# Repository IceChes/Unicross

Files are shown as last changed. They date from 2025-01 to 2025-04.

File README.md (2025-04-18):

# Unicross
Unicross is a simple 180mm cross-gantry 3d printer. It was designed to fill a niche - that being cheap cross gantry printers. The BOM cost was about $400 as of 2024, making this printer a good replacement for a Prusa Mini or other similar machine. 

Version 2 is the current usable version. Version 1 is deprecated.



There is no assembly guide, because I made this machine primarily for myself, but there are attached STEP files for the toolhead and main assembly to reference off of. A BOM is completed. I recommend you open the toolhead and assembly STEP files in your favorite CAD software and use the built-in tools to explore the model during assembly.

When I built this machine it cost about $400-450. However, the fluctuating prices of goods during the current trade crisis means I cannot provide an estimate of cost. Proceed with caution.

https://cad.onshape.com/documents/c27a3c37a85bf871058d970a/w/8efdc285a080f347fddd0032/e/d65661c6b902910ffd47d532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

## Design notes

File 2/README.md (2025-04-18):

# Printed Parts Guide

MINIMUM RECOMMENDED SETTINGS:
- Walls: 4
- Top layers: 4
- Bottom layers - 3
- Infill - 20% 3D infill (such as cubic, gyroid, etc)

# Parts
- Bed Knob: use a non-creeping filament at 100% infill. Pause the print to insert a nut. You can check the exact layer in your slicer.
- All Bed Mounting Parts: use a non-creeping filament and at least minimum settings. The BEARING HOLDER and BED MOUNT are both intended to be printed laying down on their sides.
- BLTouch Mount: use a non-creeping filament resistant to at least 60C and 100% infill.
- Bracket Plate: Use a non-creeping filament and at least minimum settings.
- Corner Bracket: Use a non-creeping filament and at least minimum settings.
- Foot: Use a non-creeping filament and at least minimum settings. You may wish to add bottom layers for extra ruggedness.
- LCD Mount: Use any filament at any sufficiently strong settings.
- Limiters: Use a non-creeping filament and at least minimal settings.
- Long and Short Mounts: Use a non-creeping filament resistant to at least 60C, 6 walls, 6 top layers, and 3 bottom layers with 40% 3D infill.
- Paneling Parts: Use any filament and sufficiently strong settings.
- Rod Block: Use any non-creeping filament with 6 walls, 6 top layers, 6 bottom layers, and 60% 3D infill.
- Tensioner: Use any non-creeping filament and 100% infill. Ensure very good layer adhesion.
- Toolhead Cable Clamp: Use any filament with at least minimal settings.
- Toolhead Hotend Clamp: Use any filament resistant to at least 60C and minimal settings.
- Toolhead: Use any filament resistant to at least 60C, 6 walls, 6 top layers, 6 bottom layers, and 40% 3D infill.
- Z Arm: Use any non-creeping filament with at least minimal settings.
- Z Motor Mount: Use any non-creeping filament resistant to at least 60C and minimal settings.

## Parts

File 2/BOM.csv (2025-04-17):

Part | Quant. | Link
2020 extrusion 350mm | 8 | https://www.aliexpress.us/item/3256805051854714.html
KP3S bed | 1 | N/A (I genuinely do not know where to buy these since Kingroon discontinued the KP3s)
4240 motor | 5 | https://www.amazon.com/STEPPERONLINE-Stepper-63-74oz-Connector-Extruder/dp/B07LCHHQ97
LM8UU bearing | 8 | https://www.aliexpress.us/item/2251832657203612.html
LM8LUU bearing | 2 | https://www.aliexpress.us/item/2255800936019514.html
250x8mm linear rod | 4 | https://www.aliexpress.us/item/3256801194605508.html
300x8mm linear rod | 6 | https://www.aliexpress.us/item/3256801194605508.html
T8 nut | 2 | N/A (included with leadscrew)
T8 leadscrew 250mm | 2 | https://www.aliexpress.us/item/2255801146318191.html
GT2 belt | ~5M | https://www.aliexpress.us/item/3256806120793282.html
750mm GT2 belt | 1 | https://www.aliexpress.us/item/3256804262911780.html
20T 5mm bore GT2 pulley | 5 | https://www.aliexpress.us/item/2251832808788159.html
20T 5mm bore GT2 idler | 6 | https://www.aliexpress.us/item/2251832539995194.html
180mm PEI sheet | 1 | https://www.aliexpress.us/item/3256805641662701.html
30T 8mm bore GT2 pulley | 2 | https://www.aliexpress.us/item/3256805593092055.html
608 bearing | 2 | https://www.aliexpress.us/item/3256801626904419.html
Electronic component | Quant. | Link
BigTreeTech SKR E3 Mini 3.0 | 1 | https://www.aliexpress.us/item/3256805861115217.html
Meanwell LRS-350-24 | 1 | https://www.aliexpress.us/item/3256806958274247.html
Raspberry Pi <2-5> | 1 | N/A (please check for availability in various places)
IEC fused power socket | 1 | https://www.aliexpress.us/item/2251832643407093.html
16awg stranded wire | N/A | N/A (everyone has their favorite brand or own supply)
22awg stranded wire | N/A | N/A (everyone has their favorite brand or own supply)
Buck converter | 1 | https://www.aliexpress.us/item/3256804718557368.html
Fan MOSFET [optional] | 1 | https://www.aliexpress.us/item/3256805264005227.html
Parallel board | 2 | https://www.aliexpress.us/item/3256803393452783.html
Stepper cable | 5 | https://www.aliexpress.us/item/3256804466627797.html
Toolhead component | Quant. | Link
Dragon hotend | 1 | https://www.aliexpress.us/item/3256804340965950.html
Sherpa mini extruder | 1 | https://www.aliexpress.us/item/3256802301412640.html
4010 blower fan | 2 | https://www.aliexpress.us/item/2251832612319325.html
Cartridge thermistor | 1 | https://www.aliexpress.us/item/3256805987471638.html
24V heater cartridge | 1 | https://www.aliexpress.us/item/2251832630477143.html
4010 axial fan | 1 | https://www.aliexpress.us/item/3256804770149410.html
BLTouch (or substitute) | 1 | https://www.aliexpress.us/item/2251832763135773.html
Hardware piece
M5x10 bolt | 2 packs | https://www.aliexpress.us/item/2251832708216186.html
M5 nut | 1 pack | https://www.aliexpress.us/item/3256803624749385.html
M5 T-nut | 3 packs | https://www.aliexpress.us/item/3256801437020797.html
M3 screw set | 1 | https://www.aliexpress.us/item/3256806736020361.html

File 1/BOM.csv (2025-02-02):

Part | Quant. | Unit. | Ext. | Link
2020 extrusion 350mm | 8 | $13.45/4 | 26.9 | https://www.aliexpress.us/item/3256805051854714.html
KP3S bed | 1 | $22.99/1 | 22.99 | https://www.aliexpress.us/item/2255800343160168.html
4240 motor | 5 | $48/5 | 48 | https://www.amazon.com/STEPPERONLINE-Stepper-63-74oz-Connector-Extruder/dp/B07LCHHQ97
LM8UU bearing | 8 | $6.70/4 | 13.4 | https://www.aliexpress.us/item/2251832657203612.html
LM8LUU bearing | 2 | $7.16/2 | 7.16 | https://www.aliexpress.us/item/2255800936019514.html
250x8mm linear rod | 4 | $3.36/1 | 13.44 | https://www.aliexpress.us/item/3256801194605508.html
300x8mm linear rod | 6 | $4.04/1 | 24.24 | https://www.aliexpress.us/item/3256801194605508.html
T8 nut | 2 |  |  | N/A (included with leadscrew)
T8 leadscrew 250mm | 2 | $3.69/1 | 7.38 | https://www.aliexpress.us/item/2255801146318191.html
GT2 belt | ~5M | $11.99/5M | 11.99 | https://www.aliexpress.us/item/3256806120793282.html
730mm GT2 belt | 1 | $1.42 | 1.42 | https://www.aliexpress.us/item/3256804262911780.html
20T 5mm bore GT2 pulley | 5 | $6.79/5 | 6.79 | https://www.aliexpress.us/item/2251832808788159.html
20T 5mm bore GT2 idler | 6 | $15.29/10 | 15.29 | https://www.aliexpress.us/item/2251832539995194.html
180mm PEI sheet [optional, bed comes with a sheet] | 1 | $15.36/1 | 15.36 | https://www.aliexpress.us/item/3256805641662701.html
30T 8mm bore GT2 pulley | 2 | $2/1 | 4 | https://www.aliexpress.us/item/3256805593092055.html
608 bearing | 2 | $2.66/10 | 2.66 | https://www.aliexpress.us/item/3256801626904419.html
Electronic component | Quant. | Unit. | Ext. | Link
BigTreeTech SKR E3 Mini 3.0 | 1 | $29.40//1 | 29.4 | https://www.aliexpress.us/item/3256805861115217.html
Meanwell LRS-350-24 | 1 | $37.58/1 | 37.58 | https://www.aliexpress.us/item/3256806958274247.html
Raspberry Pi <2-5> | 1 | $35/1 | 35 | N/A (please check for availability in various places)
IEC fused power socket | 1 | $1.39/1 | 1.39 | https://www.aliexpress.us/item/2251832643407093.html
16awg stranded wire | N/A |  |  | N/A (everyone has their favorite brand or own supply)
22awg stranded wire | N/A |  |  | N/A (everyone has their favorite brand or own supply)
Buck converter | 1 | $1.25/1 | 1.25 | https://www.aliexpress.us/item/3256804718557368.html
Fan MOSFET [optional] | 1 | $1.12/1 | 1.12 | https://www.aliexpress.us/item/3256805264005227.html
Parallel board | 2 | $3.3/4 | 3.3 | https://www.aliexpress.us/item/3256803393452783.html
Stepper cable | 5 | $1.60/4 | 5.2 | https://www.aliexpress.us/item/3256804466627797.html
Toolhead component | Quant. | Unit. | Ext. | Link
Dragon hotend | 1 | $17.34/1 | 17.34 | https://www.aliexpress.us/item/3256804340965950.html
Sherpa mini extruder | 1 | $33.73/1 | 33.73 | https://www.aliexpress.us/item/3256802301412640.html
4010 blower fan | 2 | $13.09/2 | 13.09 | https://www.aliexpress.us/item/2251832612319325.html
Cartridge thermistor | 1 | $1.76/2 | 1.76 | https://www.aliexpress.us/item/3256805987471638.html
24V heater cartridge | 1 | $3.07/1 | 3.07 | https://www.aliexpress.us/item/2251832630477143.html
4010 axial fan | 1 | $4.17/1 | 4.17 | https://www.aliexpress.us/item/3256804770149410.html
BLTouch (or substitute) | 1 | $10.94/1 | 10.94 | https://www.aliexpress.us/item/2251832763135773.html
Hardware piece
M5x10 bolt | 2 packs | $4.62/pck | 9.24 | https://www.aliexpress.us/item/2251832708216186.html
M5 nut | 1 pack | $3.69/pck | 3.69 | https://www.aliexpress.us/item/3256803624749385.html
M5 T-nut | 3 packs | $1.42/pck | 4.26 | https://www.aliexpress.us/item/3256801437020797.html
M3 screw set | 1 | $5/1 | 5 | https://www.aliexpress.us/item/3256806736020361.html
 |  |  | 419.87

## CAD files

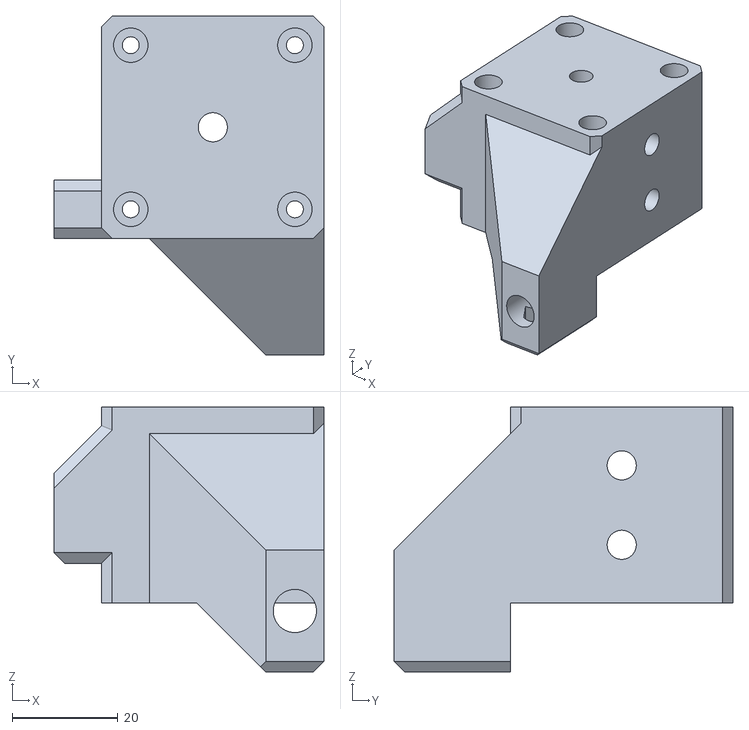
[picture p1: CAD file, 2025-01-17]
1/Files/STL/Motor Mount - Short Mount.stl
51.0 x 64.0 x 50.0

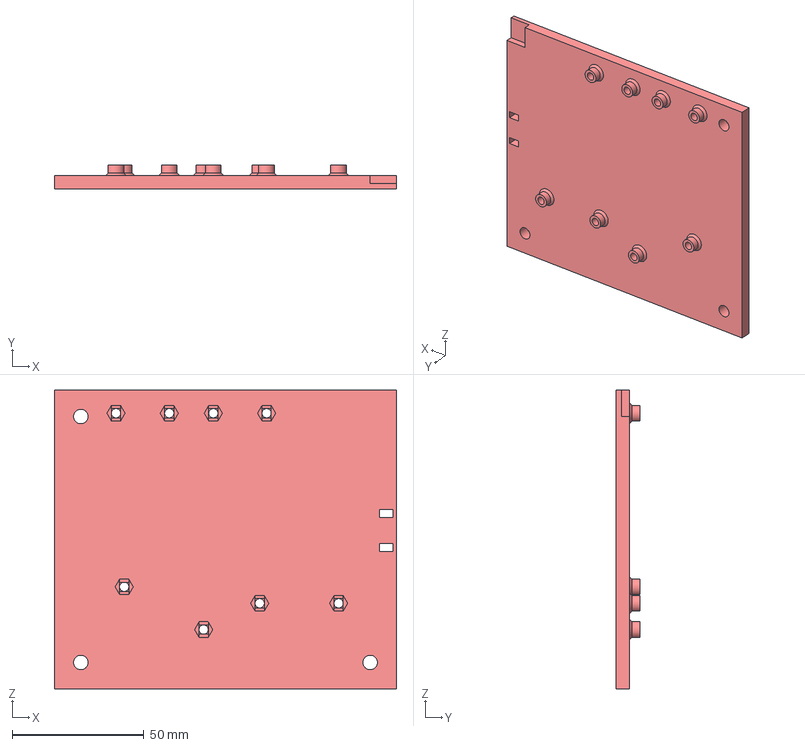
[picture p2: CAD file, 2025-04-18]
2/Files/Paneling - Bottom Right.step
130.0 x 9.00 x 113.5 mm

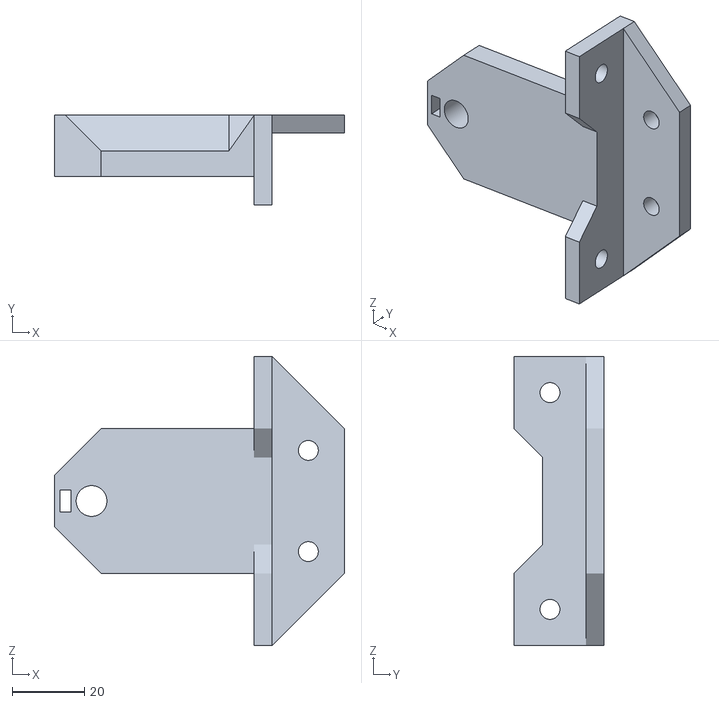
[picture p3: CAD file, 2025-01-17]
1/Files/STL/Z Rod Arm.stl
80.2 x 25.0 x 80.0

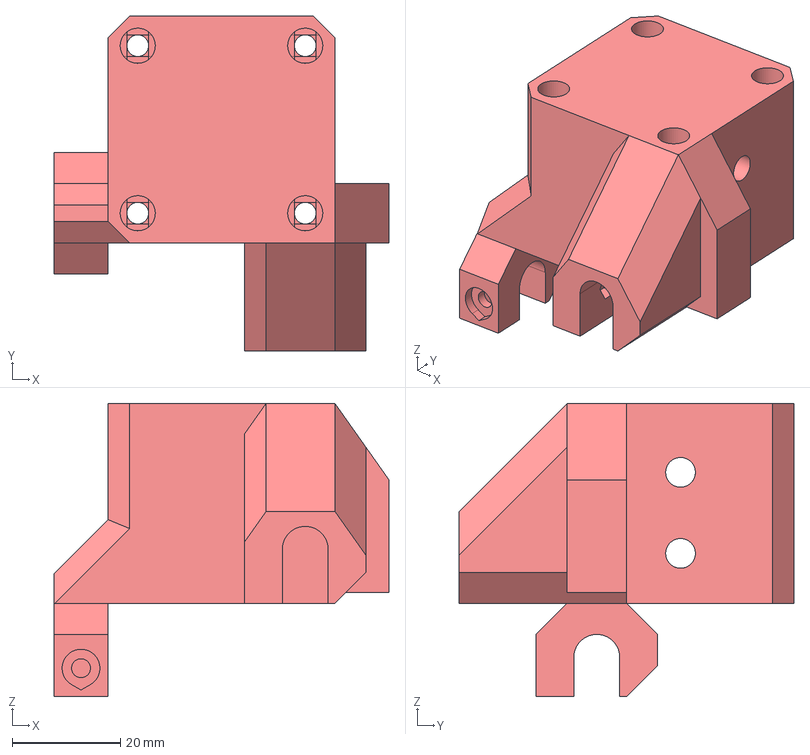
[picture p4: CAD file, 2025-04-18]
2/Files/Short Mount.step
62.0 x 62.0 x 54.2 mm

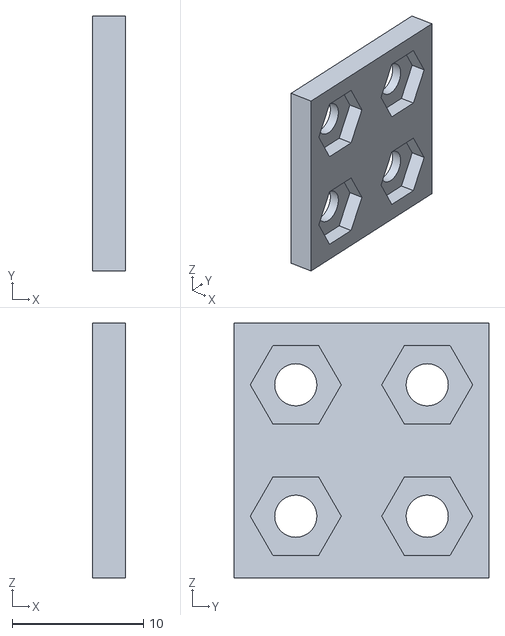
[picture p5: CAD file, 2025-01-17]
1/Files/STL/Panelling - Connector.stl
2.50 x 19.4 x 19.4

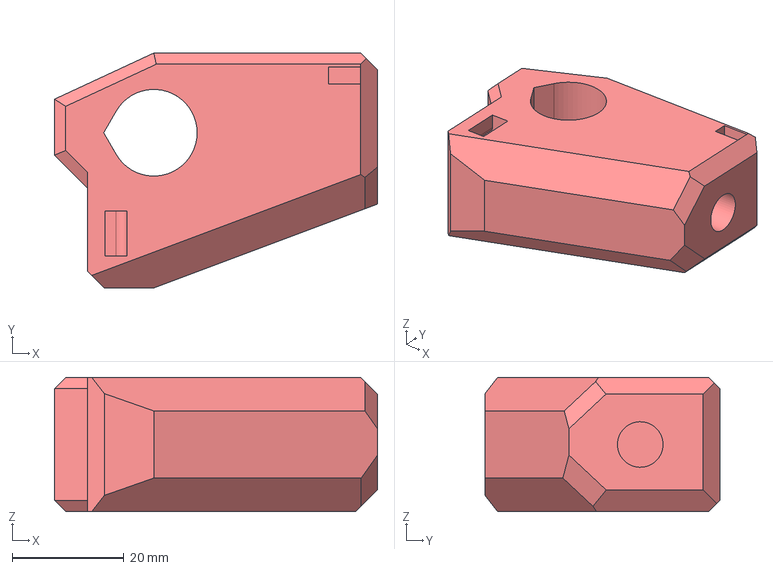
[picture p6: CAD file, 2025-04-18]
2/Files/Rod Block.step
57.8 x 42.0 x 24.0 mm

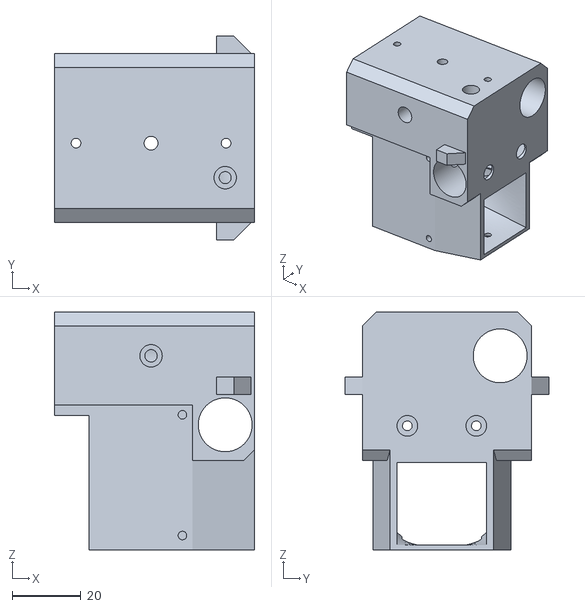
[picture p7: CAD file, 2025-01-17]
1/Files/STL/Toolhead.stl
58.0 x 59.0 x 69.0

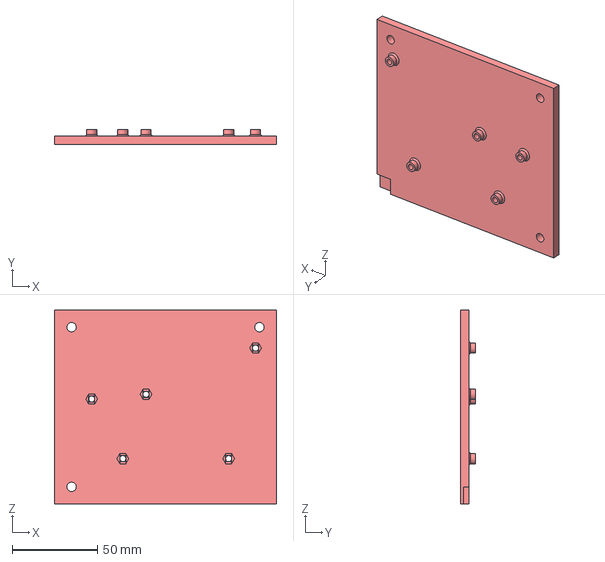
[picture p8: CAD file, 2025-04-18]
2/Files/Paneling - Top Right.step
130.0 x 9.00 x 113.5 mm

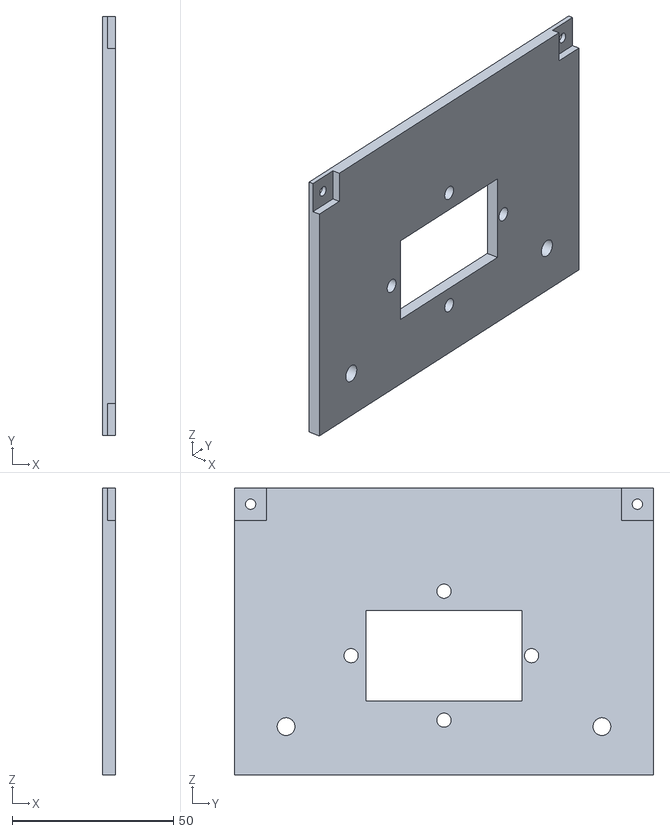
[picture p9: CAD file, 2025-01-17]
1/Files/STL/Panelling - Bottom Mid.stl
4.00 x 130.0 x 89.0

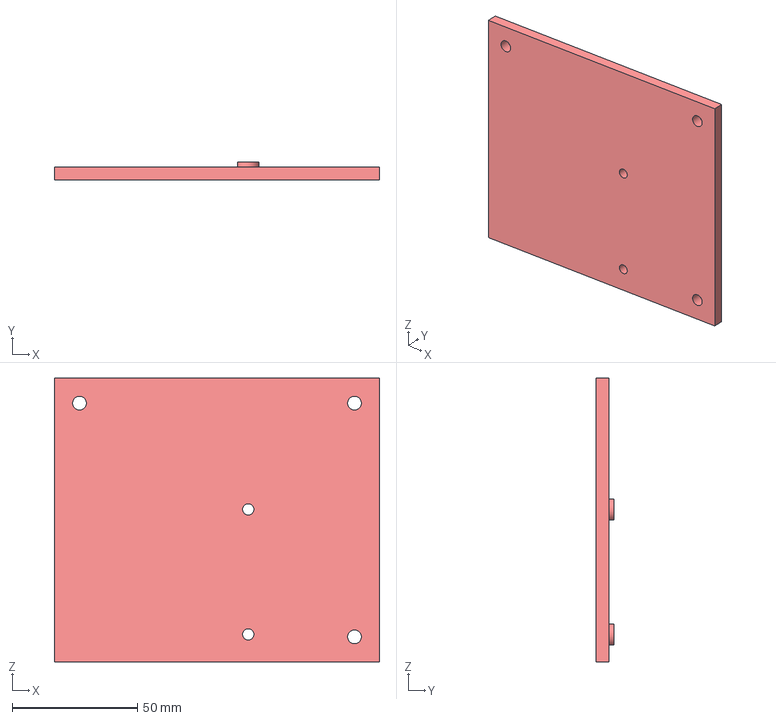
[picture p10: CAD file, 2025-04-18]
2/Files/Paneling - Top Left.step
130.0 x 7.00 x 113.5 mm

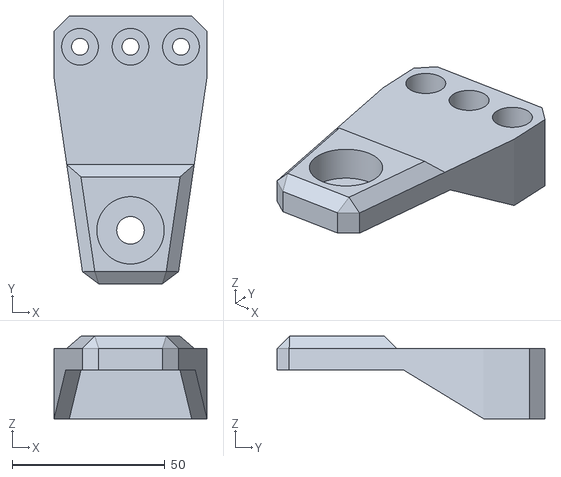
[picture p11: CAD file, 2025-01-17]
1/Files/STL/Z Axis - Bearing Block.stl
50.0 x 87.5 x 27.0

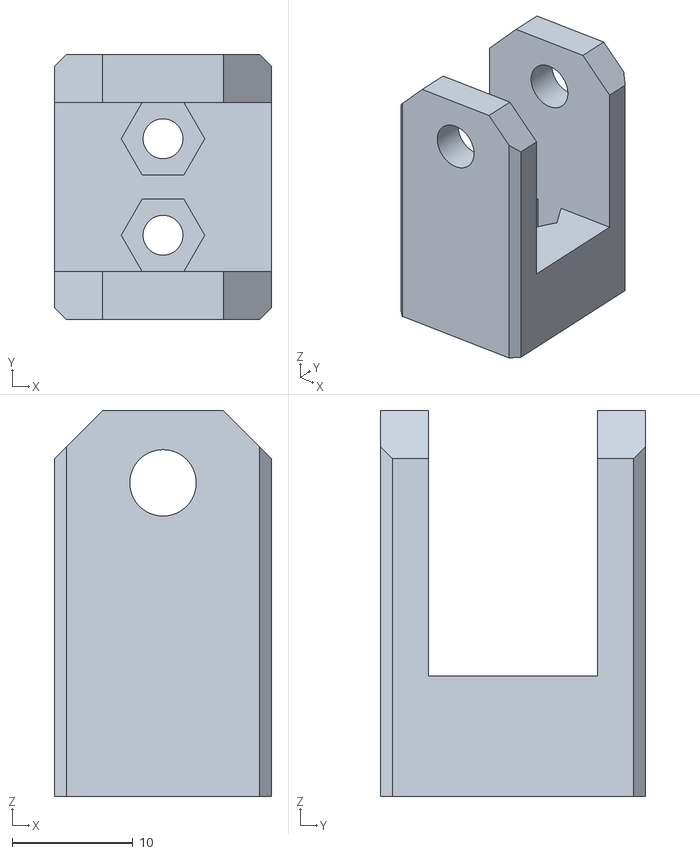
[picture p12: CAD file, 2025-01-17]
1/Files/STL/XY Tensioner.stl
18.0 x 22.0 x 32.0

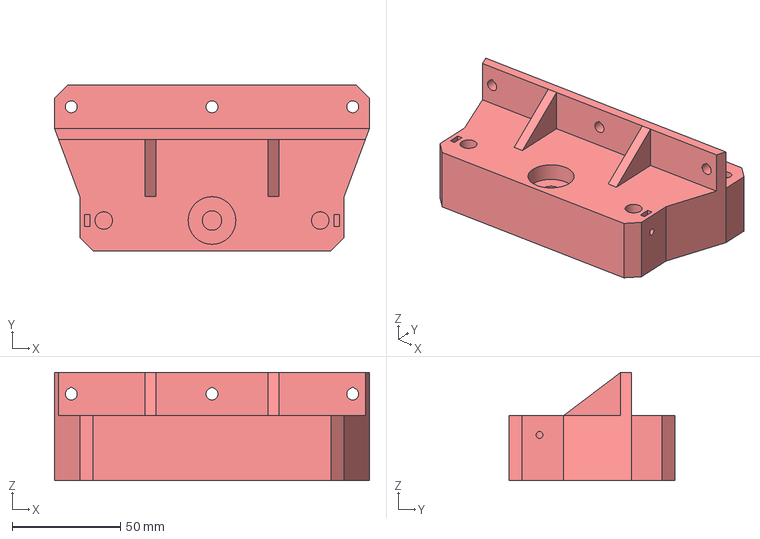
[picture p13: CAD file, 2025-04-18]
2/Files/Bed Mounting - Base Block.step
145.5 x 76.5 x 50.0 mm

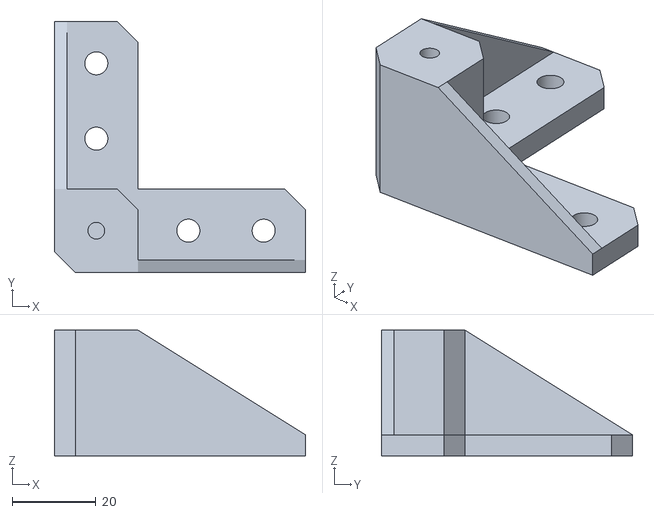
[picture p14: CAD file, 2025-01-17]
1/Files/STL/Foot.stl
60.0 x 60.0 x 30.0

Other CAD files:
2/Files/Paneling - Top Mid.step
2/Files/Paneling - Bottom Left.step
1/Files/STL/BLTouch Mount.stl
2/Files/Paneling - Bottom Mid.step
1/Files/STL/4010 Blower - Duct - Left.stl
1/Files/STL/4010 Blower - Duct - Right.stl
1/Files/STL/Corner Bracket.stl
1/Files/STL/LM8UU - Rod Block.stl
1/Files/STL/Motor Mount - Long Mount.stl
1/Files/STL/Panelling - Bottom Left.stl
1/Files/STL/Panelling - Bottom Right.stl
1/Files/STL/Panelling - Panel Bracket.stl
1/Files/STL/Panelling - Top Left.stl
1/Files/STL/Panelling - Top Mid.stl
1/Files/STL/Panelling - Top Right.stl
1/Files/STL/Toolhead Hotend Clamp.stl
1/Files/STL/Z Axis - Bed Bracket.stl
1/Files/STL/Z Axis - Z Base Block.stl
1/Files/STL/Z Motor Mount.stl
2/Files/BLTouch Mount.step
2/Files/Bed Knob.step
2/Files/Bed Mounting - Bearing Holder.step
2/Files/Bed Mounting - Bed Mount.step
2/Files/Bracket Plate.step
2/Files/Corner Bracket.step
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

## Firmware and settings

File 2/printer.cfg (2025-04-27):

[include macros.cfg]
[include mainsail.cfg]
[virtual_sdcard]
path: /home/pi/printer_data/gcodes
on_error_gcode: CANCEL_PRINT

[stepper_x]
step_pin: PB13
dir_pin: !PB12
enable_pin: !PB14
microsteps: 16
rotation_distance: 40
position_endstop: -6
position_max: 185
position_min: -6
homing_speed: 20
endstop_pin: tmc2209_stepper_x:virtual_endstop
homing_retract_dist: 0

[tmc2209 stepper_x]
uart_pin: PC11
tx_pin: PC10
uart_address: 0
run_current: 1
interpolate: False
stealthchop_threshold: 999999
diag_pin: ^PC0
driver_SGTHRS: 26

[stepper_y]
step_pin: PB10
dir_pin: PB2
enable_pin: !PB11
microsteps: 16
rotation_distance: 40
position_endstop: -3
position_max: 185
position_min: -3
homing_speed: 20
endstop_pin: tmc2209_stepper_y:virtual_endstop
homing_retract_dist: 0

[tmc2209 stepper_y]
uart_pin: PC11
tx_pin: PC10
uart_address: 2
run_current: 1
interpolate: False
stealthchop_threshold: 999999
diag_pin: ^PC1
driver_SGTHRS: 26

[stepper_z]
step_pin: PB0
dir_pin: !PC5
enable_pin: !PB1
microsteps: 16
rotation_distance: 8
endstop_pin: probe:z_virtual_endstop
#position_endstop: 0.0
position_max: 250
position_min: -10
homing_speed: 10
gear_ratio: 3:2

[tmc2209 stepper_z]
uart_pin: PC11
tx_pin: PC10
uart_address: 1
run_current: 1
interpolate: True
stealthchop_threshold: 0

[extruder]
step_pin: PB3
dir_pin: !PB4
enable_pin: !PD1
microsteps: 8
rotation_distance: 22.68776
gear_ratio: 50:8
nozzle_diameter: 0.4
filament_diameter: 1.75
heater_pin: PC8
sensor_type: ATC Semitec 104GT-2
sensor_pin: PA0
#control: pid
#pid_Kp: 21.527
#pid_Ki: 1.063
#pid_Kd: 108.982
min_temp: 0
max_temp: 300
max_extrude_only_distance: 1000
pressure_advance: 0.0925

[tmc2209 extruder]
uart_pin: PC11
tx_pin: PC10
uart_address: 3
run_current: 0.7
stealthchop_threshold: 999999

[heater_bed]
heater_pin: PC9
sensor_type: ATC Semitec 104GT-2
sensor_pin: PC4
#control: pid
#pid_Kp: 54.027
#pid_Ki: 0.770
#pid_Kd: 948.182
min_temp: 0
max_temp: 130

[heater_fan nozzle_cooling_fan]
pin: PC6

[fan]
pin: PC7

[mcu]
serial: /dev/serial/by-id/usb-Klipper_stm32g0b1xx_4100290008504B5735313920-if00

[printer]
kinematics: cartesian
max_velocity: 250
max_accel: 1000
max_z_velocity: 15
max_z_accel: 100
square_corner_velocity: 30


[bltouch]
sensor_pin: ^PC14
control_pin: PA1
stow_on_each_sample: False
probe_with_touch_mode: True
pin_up_reports_not_triggered: True
pin_up_touch_mode_reports_triggered: True

x_offset: 0
y_offset: 37.5
#z_offset: 0

[verify_heater extruder]
max_error: 300
check_gain_time: 90
hysteresis: 8
heating_gain: 2

[bed_mesh]
speed: 300
horizontal_move_z: 8
mesh_min: 40, 40
mesh_max: 140, 140
probe_count: 5, 5
mesh_pps: 3, 3
algorithm: bicubic
fade_start: 1
fade_end: 10
fade_target: 0

[homing_override]
gcode:

    FORCE_MOVE STEPPER=stepper_z DISTANCE=3 VELOCITY=10 
    
    SET_TMC_CURRENT STEPPER=stepper_x CURRENT=1.000
    SET_TMC_CURRENT STEPPER=stepper_y CURRENT=1.000

    G28 Y
    G1 Y10
    G28 X 
    G1 X10
    G1 X90 Y52.5 ; Change the X and Y coordinates to the center of your print bed
    G28 Z
    
    SET_TMC_CURRENT STEPPER=stepper_x CURRENT=1.400
    SET_TMC_CURRENT STEPPER=stepper_y CURRENT=1.400 


[display]
lcd_type: st7920
cs_pin: EXP1_7
sclk_pin: EXP1_6
sid_pin: EXP1_8
encoder_pins: ^EXP1_5, ^EXP1_3
click_pin: ^!EXP1_2

[board_pins]
aliases:

    EXP1_1=PB5,  EXP1_3=PA9,   EXP1_5=PA10, EXP1_7=PB8, EXP1_9=<GND>,
    EXP1_2=PA15, EXP1_4=<RST>, EXP1_6=PB9,  EXP1_8=PD6, EXP1_10=<5V>

[force_move]
enable_force_move = true

[idle_timeout]
gcode:
  m84
timeout: 64800

[exclude_object]

[respond]
default_type: echo
default_prefix: echo:

[save_variables]
filename: ~/printer_data/config/variables.cfg

[pause_resume]
recover_velocity: 300

#*# <---------------------- SAVE_CONFIG ---------------------->
#*# DO NOT EDIT THIS BLOCK OR BELOW. The contents are auto-generated.
#*#
#*# [extruder]
#*# control = pid
#*# pid_kp = 18.981
#*# pid_ki = 1.291
#*# pid_kd = 69.754
#*#
#*# [bltouch]
#*# z_offset = 2.400
#*#
#*# [bed_mesh default]
#*# version = 1
#*# points =
#*# 	0.068333, 0.079167, 0.077500, 0.088333, 0.095833
#*# 	0.052500, 0.035833, 0.056667, 0.050833, 0.041667
#*# 	0.002500, -0.014167, -0.008333, -0.012500, -0.005833
#*# 	-0.064167, -0.057500, -0.074167, -0.080000, -0.076667
#*# 	-0.139167, -0.151667, -0.170833, -0.149167, -0.138333
#*# x_count = 5
#*# y_count = 5
#*# mesh_x_pps = 3
#*# mesh_y_pps = 3
#*# algo = bicubic
#*# tension = 0.2
#*# min_x = 40.0
#*# max_x = 140.0
#*# min_y = 40.0
#*# max_y = 140.0
#*#
#*# [heater_bed]
#*# control = pid
#*# pid_kp = 66.213
#*# pid_ki = 1.752
#*# pid_kd = 625.717

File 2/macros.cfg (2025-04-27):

[gcode_macro SMART_HOME]
gcode:
    {% if printer.toolhead.homed_axes != "xyz" %}
        G28
    {% endif %}

[gcode_macro PARK]
description: Park the toolhead at the origin
gcode:
  G90
  G0 X60 Y180 F3000

[gcode_macro CHANGE_FILAMENT_BEGIN]
description: Begin the change filament wizard
gcode:

  {% set svv = printer.save_variables.variables %}
  {% set unload_temp = svv.loaded_filament_temp|default(240)|int %}

  M104 S{unload_temp}
    
  SMART_HOME
    
  PARK

  RESPOND TYPE=echo MSG="Waiting for heat to unload filament."
  
  M109 S{unload_temp}
  M83
  G92 E0
    
  RESPOND TYPE=command MSG="action:prompt_begin Retract filament"
  RESPOND TYPE=command MSG="action:prompt_text Full retract removes filament from the hotend. Small retract removes a bit more if the full retract wasn't enough."
    
  RESPOND TYPE=command MSG="action:prompt_button_group_start"
  RESPOND TYPE=command MSG="action:prompt_button full retract|G0 E-120 F1000|primary"
  RESPOND TYPE=command MSG="action:prompt_button small retract|G0 E-5 F1000|primary"
  RESPOND TYPE=command MSG="action:prompt_button_group_end"
    
  RESPOND TYPE=command MSG="action:prompt_footer_button NEXT|CHANGE_FILAMENT_SELECT|primary"
    
  RESPOND TYPE=command MSG="action:prompt_show"

[gcode_macro CHANGE_FILAMENT_SELECT]
description: Begin the filament select wizard
gcode:
  
  RESPOND TYPE=command MSG=action:prompt_end
  
  RESPOND TYPE=command MSG="action:prompt_begin Select filament"
  RESPOND TYPE=command MSG="action:prompt_text Choose which filament is being loaded. The OTHER option will use 240C as the load/unload temperature."
    
  RESPOND TYPE=command MSG="action:prompt_button_group_start"
  RESPOND TYPE=command MSG="action:prompt_button PLA|SAVE_VARIABLE VARIABLE=loaded_filament_temp VALUE={210}|primary"
  RESPOND TYPE=command MSG="action:prompt_button PETG|SAVE_VARIABLE VARIABLE=loaded_filament_temp VALUE={240}|primary"
  RESPOND TYPE=command MSG="action:prompt_button ABS/ASA|SAVE_VARIABLE VARIABLE=loaded_filament_temp VALUE={250}|primary"
  RESPOND TYPE=command MSG="action:prompt_button_group_end"
  RESPOND TYPE=command MSG="action:prompt_button_group_start"
  RESPOND TYPE=command MSG="action:prompt_button Nylon|SAVE_VARIABLE VARIABLE=loaded_filament_temp VALUE={270}|primary"
  RESPOND TYPE=command MSG="action:prompt_button TPU|SAVE_VARIABLE VARIABLE=loaded_filament_temp VALUE={200}|primary"
  RESPOND TYPE=command MSG="action:prompt_button Other|SAVE_VARIABLE VARIABLE=loaded_filament_temp VALUE={240}|primary"
  RESPOND TYPE=command MSG="action:prompt_button_group_end"
    
  RESPOND TYPE=command MSG="action:prompt_footer_button NEXT|CHANGE_FILAMENT_LOAD|primary"

  RESPOND TYPE=command MSG="action:prompt_show"


[gcode_macro CHANGE_FILAMENT_LOAD]
description: Begin the load filament wizard
gcode:
  
  {% set svv = printer.save_variables.variables %}
  {% set load_temp = svv.loaded_filament_temp|default(240)|int %}

  M104 S{load_temp}

  SMART_HOME
    
  PARK
  
  RESPOND TYPE=command MSG=action:prompt_end
  RESPOND TYPE=echo MSG="Waiting for heat to load filament."

    
  M109 S{load_temp}

  M83
  
  RESPOND TYPE=command MSG="action:prompt_begin Load filament"
  RESPOND TYPE=command MSG="action:prompt_text Push filament up to the extruder gears, then press LOAD. Use PURGE as needed until color is correct."
    
  RESPOND TYPE=command MSG="action:prompt_button_group_start"
  RESPOND TYPE=command MSG="action:prompt_button LOAD|G0 E120 F1000|primary"
  RESPOND TYPE=command MSG="action:prompt_button PURGE|G0 E20 F250|primary"
  RESPOND TYPE=command MSG="action:prompt_button_group_end"
    
  RESPOND TYPE=command MSG="action:prompt_footer_button COOL NOZZLE|M104 S0|primary"

  RESPOND TYPE=command MSG="action:prompt_show"
  
[gcode_macro WLED_ON]
description: Turn WLED strip on using optional preset
gcode:
  {% set strip = params.STRIP|default("chamber")|string %}
  {% set preset = params.PRESET|default(4)|int %}

  {action_call_remote_method("set_wled_state",
                             strip=strip,
                             state=True,
                             preset=preset)}

[gcode_macro WLED_WARM_LIGHT]
description: Switch to the "warm lights" WLED preset
gcode:
  WLED_ON STRIP=chamber PRESET=3

[gcode_macro WLED_COOL_LIGHT]
description: Switch to the "cool lights" WLED preset
gcode:
  WLED_ON STRIP=chamber PRESET=2
                             
[gcode_macro WLED_OFF]
description: Set WLED strip to 0 brightness
gcode:
  WLED_ON STRIP=chamber PRESET=4

[gcode_macro CHANGE_NOZZLE]
description: Initiate a nozzle change
gcode: 

  {% set svv = printer.save_variables.variables %}
  {% set load_temp = svv.nozzle_size|default(0.4)|int %}

  {% set svv = printer.save_variables.variables %}
  {% set unload_temp = svv.loaded_filament_temp|default(240)|int %}
  
  SMART_HOME
  PARK
  G0 Z80 F3000

  RESPOND TYPE=echo MSG="Waiting for heat to unload filament."

  M104 S{unload_temp}
  M109 S{unload_temp}
  
  M83
  G92 E0
  G0 E-10 F1000
  M109 S280

  RESPOND TYPE=command MSG="action:prompt_begin Select nozzle size"
  RESPOND TYPE=command MSG="action:prompt_text Choose a nozzle diameter"
    
  RESPOND TYPE=command MSG="action:prompt_button_group_start"
  RESPOND TYPE=command MSG="action:prompt_button 0.2|SAVE_VARIABLE VARIABLE=nozzle_size VALUE={0.2}|primary"
  RESPOND TYPE=command MSG="action:prompt_button 0.25|SAVE_VARIABLE VARIABLE=nozzle_size VALUE={0.25}|primary"
  RESPOND TYPE=command MSG="action:prompt_button 0.4|SAVE_VARIABLE VARIABLE=nozzle_size VALUE={0.4}|primary"
  RESPOND TYPE=command MSG="action:prompt_button_group_end"
  RESPOND TYPE=command MSG="action:prompt_button_group_start"
  RESPOND TYPE=command MSG="action:prompt_button 0.5|SAVE_VARIABLE VARIABLE=nozzle_size VALUE={0.5}|primary"
  RESPOND TYPE=command MSG="action:prompt_button 0.6|SAVE_VARIABLE VARIABLE=nozzle_size VALUE={0.6}|primary"
  RESPOND TYPE=command MSG="action:prompt_button 0.8|SAVE_VARIABLE VARIABLE=nozzle_size VALUE={0.8}|primary"
  RESPOND TYPE=command MSG="action:prompt_button_group_end"
    
  RESPOND TYPE=command MSG="action:prompt_footer_button NEXT|CHANGE_NOZZLE_CHANGE|primary"

  RESPOND TYPE=command MSG="action:prompt_show"
  
[gcode_macro CHANGE_NOZZLE_CHANGE]
description: change the nozzle
gcode:

  {% set svv = printer.save_variables.variables %}
  {% set load_temp = svv.loaded_filament_temp|default(240)|int %}
  
  RESPOND TYPE=command MSG=action:prompt_end
  
  RESPOND TYPE=command MSG="action:prompt_begin Change nozzle"
  RESPOND TYPE=command MSG="action:prompt_text Press the button when nozzle change is finished."
  RESPOND TYPE=command MSG="action:prompt_footer_button FINISHED|CHANGE_NOZZLE_FINISH|primary"
    
  RESPOND TYPE=command MSG="action:prompt_show"

[gcode_macro CHANGE_NOZZLE_FINISH]
description: finish changing the nozzle
gcode:

  {% set svv = printer.save_variables.variables %}
  {% set load_temp = svv.loaded_filament_temp|default(240)|int %}

  RESPOND TYPE=command MSG=action:prompt_end
  
  RESPOND TYPE=echo MSG="Cooling..."
  M104 S{load_temp}

  RESPOND TYPE=echo MSG="Purging..."
  G0 E25 F1000

  RESPOND TYPE=echo MSG="New nozzle installed"
  M104 S0

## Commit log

2025-02-02 add BOM
    [BOM.csv]
2025-02-13 upload the latest version of my very basic cfg
    [printer.cfg]
2025-04-17 Upload V2
    [4010 Blower - Duct - Left.stl, 4010 Blower - Duct - Right.stl, BLTouch Mount.step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]
2025-04-18 Remove STL support
    [BLTouch Mount.step, BLTouch Mount.stl, Bed Knob.step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]
2025-04-18 update parts with new nut tolerances
    [Bed Mounting - Base Block.step, Bed Mounting - Bed Mount.step, Long Mount.step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]
2025-04-27 added config files - more updates soon
    [macros.cfg, printer.cfg, variables.cfg]
